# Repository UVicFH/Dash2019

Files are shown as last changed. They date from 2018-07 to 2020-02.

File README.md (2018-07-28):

# Dash2019

The purpose of this repository is to store the code and design files for the 2019 competition dash.

The newest CANduino revision will be used and the dash enclosure will house only a small PCB for the CANduino.

The project proposal, BOM, and other documentation can be found in the drive in Electrical/2018-2019/DASH

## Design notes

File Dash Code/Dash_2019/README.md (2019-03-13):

# Dashboard

This code runs the dashboard of the UVH19 vehicle. It takes the following message over CAN (bytes are in order starting at 0):

| Message | Bytes |
|---|---|
| RPM | 2 |
| 10*Coolant Temperature | 2 |
| SOC | 1 |
| Engine Running | 0.5 |
| RTD | 0.5 |
| Buzzer On | 1 |
| AMS Status | 0.5 |
| IMD Status | 0.5 |

This message should be sent at 5Hz from the supervisory controller and the message ID is defined in the defines.h file. 

It takes input from three buttons (engine start, motor start, and cockpit shutdown) and two analogs (Traction Control and Mode). These are indexed analog inputs.

It outputs to WS2812 addressable LED lights in 5 parts as shown below: 

| Name | Length |
|---|---|
| AMS Status | 1 |
| IMD Status | 1 |
| Engine Temperature | 1 |
| RPM	 | |
| Charge | 	 |

It also outputs the physical inputs over CAN in the following format at 5Hz:

| Message | Bytes | Format |
|---|---|---|
| Mode | 1 | Indexed 0-5 |
| Traction Control | 1 | 0-100 |
| Engine Start | 1 | 0/1 |
| Motor Start | 1 | 0/1 |
| CPBRB Status | 1 | 0/1 |

Please make sure the following library is installed before compiling: https://github.com/Seeed-Studio/CAN_BUS_Shield

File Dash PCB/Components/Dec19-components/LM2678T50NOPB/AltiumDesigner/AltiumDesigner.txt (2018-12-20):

# Created by Ultra Librarian Gold 8.3.15 Copyright © 1999-2018
# Frank Frank, Accelerated Designs

StartFootprints

Footprint (Name "TA07B")
Pad (Name "1") (Location -300, -441) (HoleSize 52) (Surface False) (Rotation 0) (ExpandMask 0)
PadShape (Size 72, 72) (Shape Rectangular) (Layer Top)
PadShape (Size 72, 72) (Shape Rectangular) (Layer Bottom)
PadShape (Size 72, 72) (Shape Rectangular) (Layer MidLayer)
EndPad
Pad (Name "2") (Location -250, -241) (HoleSize 52) (Surface False) (Rotation 0) (ExpandMask 0)
PadShape (Size 72, 72) (Shape Rounded) (Layer Top)
PadShape (Size 72, 72) (Shape Rounded) (Layer Bottom)
PadShape (Size 72, 72) (Shape Rounded) (Layer MidLayer)
EndPad
Pad (Name "3") (Location -200, -441) (HoleSize 52) (Surface False) (Rotation 0) (ExpandMask 0)
PadShape (Size 72, 72) (Shape Rounded) (Layer Top)
PadShape (Size 72, 72) (Shape Rounded) (Layer Bottom)
PadShape (Size 72, 72) (Shape Rounded) (Layer MidLayer)
EndPad
Pad (Name "4") (Location -150, -241) (HoleSize 52) (Surface False) (Rotation 0) (ExpandMask 0)
PadShape (Size 72, 72) (Shape Rounded) (Layer Top)
PadShape (Size 72, 72) (Shape Rounded) (Layer Bottom)
PadShape (Size 72, 72) (Shape Rounded) (Layer MidLayer)
EndPad
Pad (Name "5") (Location -100, -441) (HoleSize 52) (Surface False) (Rotation 0) (ExpandMask 0)
PadShape (Size 72, 72) (Shape Rounded) (Layer Top)
PadShape (Size 72, 72) (Shape Rounded) (Layer Bottom)
PadShape (Size 72, 72) (Shape Rounded) (Layer MidLayer)
EndPad
Pad (Name "6") (Location -50, -241) (HoleSize 52) (Surface False) (Rotation 0) (ExpandMask 0)
PadShape (Size 72, 72) (Shape Rounded) (Layer Top)
PadShape (Size 72, 72) (Shape Rounded) (Layer Bottom)
PadShape (Size 72, 72) (Shape Rounded) (Layer MidLayer)
EndPad
Pad (Name "7") (Location 0, -441) (HoleSize 52) (Surface False) (Rotation 0) (ExpandMask 0)
PadShape (Size 72, 72) (Shape Rounded) (Layer Top)
PadShape (Size 72, 72) (Shape Rounded) (Layer Bottom)
PadShape (Size 72, 72) (Shape Rounded) (Layer MidLayer)
EndPad
Line (Width 6) (Start -365, -118) (End -365, -487) (Layer Mechanical15) 
Line (Width 6) (Start -365, -487) (End 65, -487) (Layer Mechanical15) 
Line (Width 6) (Start 65, -487) (End 65, -118) (Layer Mechanical15) 
Line (Width 6) (Start 65, -118) (End -365, -118) (Layer Mechanical15) 
Polygon (PointCount 4) (Layer Mechanical15) 
Point (-365, -118)
Point (-365, -487)
Point (65, -487)
Point (65, -118)
EndPolygon
Line (Width 6) (Start -355, -173) (End 55, -173) (Layer TopOverlay) 
Line (Width 6) (Start -360, -318) (End 60, -318) (Layer TopOverlay) 
Line (Width 6) (Start 60, -318) (End 60, -123) (Layer TopOverlay) 
Line (Width 6) (Start 60, -123) (End -360, -123) (Layer TopOverlay) 
Line (Width 6) (Start -360, -123) (End -360, -318) (Layer TopOverlay) 
Arc (Width 6) (Radius 8) (Location -430, -441) (StartAngle 0) (EndAngle 360) (Layer TopOverlay) 
Line (Width 1) (Start -355, -178) (End 55, -178) (Layer Mechanical13) 
Line (Width 1) (Start -355, -313) (End 55, -313) (Layer Mechanical13) 
Line (Width 1) (Start 55, -313) (End 55, -128) (Layer Mechanical13) 
Line (Width 1) (Start 55, -128) (End -355, -128) (Layer Mechanical13) 
Line (Width 1) (Start -355, -128) (End -355, -313) (Layer Mechanical13) 
Arc (Width 0) (Radius 8) (Location -345, -303) (StartAngle 360) (EndAngle 720) (Layer Mechanical13) 
Text (Location -168.75, -165.5) (Height 25) (Width 1) (Rotation 0) (Layer Mechanical13) (Value "TAB")
Step (Name TA07B.stp)
EndFootprint

Footprint (Name "TA07Bm")
Pad (Name "1") (Location -300, -441) (HoleSize 52) (Surface False) (Rotation 0) (ExpandMask 0)
PadShape (Size 72, 72) (Shape Rectangular) (Layer Top)
PadShape (Size 72, 72) (Shape Rectangular) (Layer Bottom)
PadShape (Size 72, 72) (Shape Rectangular) (Layer MidLayer)
EndPad
Pad (Name "2") (Location -250, -241) (HoleSize 52) (Surface False) (Rotation 0) (ExpandMask 0)
PadShape (Size 72, 72) (Shape Rounded) (Layer Top)
PadShape (Size 72, 72) (Shape Rounded) (Layer Bottom)
PadShape (Size 72, 72) (Shape Rounded) (Layer MidLayer)
EndPad
Pad (Name "3") (Location -200, -441) (HoleSize 52) (Surface False) (Rotation 0) (ExpandMask 0)
PadShape (Size 72, 72) (Shape Rounded) (Layer Top)
PadShape (Size 72, 72) (Shape Rounded) (Layer Bottom)
PadShape (Size 72, 72) (Shape Rounded) (Layer MidLayer)
EndPad
Pad (Name "4") (Location -150, -241) (HoleSize 52) (Surface False) (Rotation 0) (ExpandMask 0)
PadShape (Size 72, 72) (Shape Rounded) (Layer Top)
PadShape (Size 72, 72) (Shape Rounded) (Layer Bottom)
PadShape (Size 72, 72) (Shape Rounded) (Layer MidLayer)
EndPad
Pad (Name "5") (Location -100, -441) (HoleSize 52) (Surface False) (Rotation 0) (ExpandMask 0)
PadShape (Size 72, 72) (Shape Rounded) (Layer Top)
PadShape (Size 72, 72) (Shape Rounded) (Layer Bottom)
PadShape (Size 72, 72) (Shape Rounded) (Layer MidLayer)
EndPad
Pad (Name "6") (Location -50, -241) (HoleSize 52) (Surface False) (Rotation 0) (ExpandMask 0)
PadShape (Size 72, 72) (Shape Rounded) (Layer Top)
PadShape (Size 72, 72) (Shape Rounded) (Layer Bottom)
PadShape (Size 72, 72) (Shape Rounded) (Layer MidLayer)
EndPad
Pad (Name "7") (Location 0, -441) (HoleSize 52) (Surface False) (Rotation 0) (ExpandMask 0)
PadShape (Size 72, 72) (Shape Rounded) (Layer Top)
PadShape (Size 72, 72) (Shape Rounded) (Layer Bottom)
PadShape (Size 72, 72) (Shape Rounded) (Layer MidLayer)
EndPad
Line (Width 6) (Start -365, -118) (End -365, -487) (Layer Mechanical15) 
Line (Width 6) (Start -365, -487) (End 65, -487) (Layer Mechanical15) 
Line (Width 6) (Start 65, -487) (End 65, -118) (Layer Mechanical15) 
Line (Width 6) (Start 65, -118) (End -365, -118) (Layer Mechanical15) 
Polygon (PointCount 4) (Layer Mechanical15) 
Point (-365, -118)
Point (-365, -487)
Point (65, -487)
Point (65, -118)
EndPolygon
Line (Width 6) (Start -355, -173) (End 55, -173) (Layer TopOverlay) 
Line (Width 6) (Start -360, -318) (End 60, -318) (Layer TopOverlay) 
Line (Width 6) (Start 60, -318) (End 60, -123) (Layer TopOverlay) 
Line (Width 6) (Start 60, -123) (End -360, -123) (Layer TopOverlay) 
Line (Width 6) (Start -360, -123) (End -360, -318) (Layer TopOverlay) 
Arc (Width 6) (Radius 8) (Location -430, -441) (StartAngle 0) (EndAngle 360) (Layer TopOverlay) 
Line (Width 1) (Start -355, -178) (End 55, -178) (Layer Mechanical13) 
Line (Width 1) (Start -355, -313) (End 55, -313) (Layer Mechanical13) 
Line (Width 1) (Start 55, -313) (End 55, -128) (Layer Mechanical13) 
Line (Width 1) (Start 55, -128) (End -355, -128) (Layer Mechanical13) 
Line (Width 1) (Start -355, -128) (End -355, -313) (Layer Mechanical13) 
Arc (Width 0) (Radius 8) (Location -345, -303) (StartAngle 360) (EndAngle 720) (Layer Mechanical13) 
Text (Location -168.75, -165.5) (Height 25) (Width 1) (Rotation 0) (Layer Mechanical13) (Value "TAB")
Step (Name TA07Bm.stp)
EndFootprint

Footprint (Name "TA07Bl")
Pad (Name "1") (Location -300, -441) (HoleSize 52) (Surface False) (Rotation 0) (ExpandMask 0)
PadShape (Size 72, 72) (Shape Rectangular) (Layer Top)
PadShape (Size 72, 72) (Shape Rectangular) (Layer Bottom)
PadShape (Size 72, 72) (Shape Rectangular) (Layer MidLayer)
EndPad
Pad (Name "2") (Location -250, -241) (HoleSize 52) (Surface False) (Rotation 0) (ExpandMask 0)
PadShape (Size 72, 72) (Shape Rounded) (Layer Top)
PadShape (Size 72, 72) (Shape Rounded) (Layer Bottom)
PadShape (Size 72, 72) (Shape Rounded) (Layer MidLayer)
EndPad
Pad (Name "3") (Location -200, -441) (HoleSize 52) (Surface False) (Rotation 0) (ExpandMask 0)
PadShape (Size 72, 72) (Shape Rounded) (Layer Top)
PadShape (Size 72, 72) (Shape Rounded) (Layer Bottom)
PadShape (Size 72, 72) (Shape Rounded) (Layer MidLayer)
EndPad
Pad (Name "4") (Location -150, -241) (HoleSize 52) (Surface False) (Rotation 0) (ExpandMask 0)
PadShape (Size 72, 72) (Shape Rounded) (Layer Top)
PadShape (Size 72, 72) (Shape Rounded) (Layer Bottom)
PadShape (Size 72, 72) (Shape Rounded) (Layer MidLayer)
EndPad
Pad (Name "5") (Location -100, -441) (HoleSize 52) (Surface False) (Rotation 0) (ExpandMask 0)
PadShape (Size 72, 72) (Shape Rounded) (Layer Top)
PadShape (Size 72, 72) (Shape Rounded) (Layer Bottom)
PadShape (Size 72, 72) (Shape Rounded) (Layer MidLayer)
EndPad
Pad (Name "6") (Location -50, -241) (HoleSize 52) (Surface False) (Rotation 0) (ExpandMask 0)
PadShape (Size 72, 72) (Shape Rounded) (Layer Top)
PadShape (Size 72, 72) (Shape Rounded) (Layer Bottom)
PadShape (Size 72, 72) (Shape Rounded) (Layer MidLayer)
EndPad
Pad (Name "7") (Location 0, -441) (HoleSize 52) (Surface False) (Rotation 0) (ExpandMask 0)
PadShape (Size 72, 72) (Shape Rounded) (Layer Top)
PadShape (Size 72, 72) (Shape Rounded) (Layer Bottom)
PadShape (Size 72, 72) (Shape Rounded) (Layer MidLayer)
EndPad
Line (Width 6) (Start -365, -118) (End -365, -487) (Layer Mechanical15) 
Line (Width 6) (Start -365, -487) (End 65, -487) (Layer Mechanical15) 
Line (Width 6) (Start 65, -487) (End 65, -118) (Layer Mechanical15) 
Line (Width 6) (Start 65, -118) (End -365, -118) (Layer Mechanical15) 
Polygon (PointCount 4) (Layer Mechanical15) 
Point (-365, -118)
Point (-365, -487)
Point (65, -487)
Point (65, -118)
EndPolygon
Line (Width 6) (Start -355, -173) (End 55, -173) (Layer TopOverlay) 
Line (Width 6) (Start -360, -318) (End 60, -318) (Layer TopOverlay) 
Line (Width 6) (Start 60, -318) (End 60, -123) (Layer TopOverlay) 
Line (Width 6) (Start 60, -123) (End -360, -123) (Layer TopOverlay) 
Line (Width 6) (Start -360, -123) (End -360, -318) (Layer TopOverlay) 
Arc (Width 6) (Radius 8) (Location -430, -441) (StartAngle 0) (EndAngle 360) (Layer TopOverlay) 
Line (Width 1) (Start -355, -178) (End 55, -178) (Layer Mechanical13) 
Line (Width 1) (Start -355, -313) (End 55, -313) (Layer Mechanical13) 
Line (Width 1) (Start 55, -313) (End 55, -128) (Layer Mechanical13) 
Line (Width 1) (Start 55, -128) (End -355, -128) (Layer Mechanical13) 
Line (Width 1) (Start -355, -128) (End -355, -313) (Layer Mechanical13) 
Arc (Width 0) (Radius 8) (Location -345, -303) (StartAngle 360) (EndAngle 720) (Layer Mechanical13) 
Text (Location -168.75, -165.5) (Height 25) (Width 1) (Rotation 0) (Layer Mechanical13) (Value "TAB")
Step (Name TA07Bl.stp)
EndFootprint
EndFootprints

StartComponents

Component (Name "LM2678T-5.0/NOPB") (PartCount 1) (DesPrefix "U?")
Pin (Location 300, 0) (Rotation 180) (PinType Output) (Length 300) (Width 0) (Designator Visible "1") (Name Visible "SW") (PinSwap 0) (PartSwap 0) (PinSeq 1) (Part 1)
Pin (Location 300, -100) (Rotation 180) (PinType Input) (Length 300) (Width 0) (Designator Visible "2") (Name Visible "Vin") (PinSwap 0) (PartSwap 0) (PinSeq 2) (Part 1)
Pin (Location 300, -200) (Rotation 180) (PinType Passive) (Length 300) (Width 0) (Designator Visible "3") (Name Visible "BOOST") (PinSwap 0) (PartSwap 0) (PinSeq 3) (Part 1)
Pin (Location 2500, -300) (Rotation 0) (PinType Passive) (Length 300) (Width 0) (Designator Visible "4") (Name Visible "GND") (PinSwap 0) (PartSwap 0) (PinSeq 4) (Part 1)
Pin (Location 2500, -200) (Rotation 0) (PinType Passive) (Length 300) (Width 0) (Designator Visible "5") (Name Visible "NC") (PinSwap 0) (PartSwap 0) (PinSeq 5) (Part 1)
Pin (Location 2500, -100) (Rotation 0) (PinType Passive) (Length 300) (Width 0) (Designator Visible "6") (Name Visible "FB") (PinSwap 0) (PartSwap 0) (PinSeq 6) (Part 1)
Pin (Location 2500, 0) (Rotation 0) (PinType Passive) (Length 300) (Width 0) (Designator Visible "7") (Name Visible "*ON/OFF") (PinSwap 0) (PartSwap 0) (PinSeq 7) (Part 1)
Rectangle (Width 5) (Start 300, 200) (End 2500, -500) (Part 1)
Parameter (Name "Manufacturer_Part_Number") (Location 0, 0) (Height 50) (Rotation 0) (Justification Center) (Value "LM2678T-5.0/NOPB") (Part 1)
Parameter (Name "Vendor") (Location 0, 0) (Height 50) (Rotation 0) (Justification Center) (Value "Texas Instruments") (Part 1)
Parameter (Name "Built_By") (Location 0, 0) (Height 50) (Rotation 0) (Justification Center) (Value "EMA_UL_Team") (Part 1)
Parameter (Name "RefDes") (Location 1400, 400) (Height 82) (Rotation 0) (Justification Center) (Value "RefDes") (Part 1)
Parameter (Name "Type") (Location 1400, 300) (Height 82) (Rotation 0) (Justification Center) (Value "DEV") (Part 1)
Parameter (Name "Value") (Location 1400, 300) (Height 82) (Rotation 0) (Justification Center) (Value "Value") (Part 1)
Parameter (Name "C") (Location 0, 0) (Height 1) (Rotation 0) (Justification Center) (Value "Copyright (C) 2015 Accelerated Designs. All rights reserved") (Part 1)
Comment (Value "Part Number: LM2678T-5.0/NOPB") (Part 1)
Footprint (Name "TA07B")
EndComponent
EndComponents

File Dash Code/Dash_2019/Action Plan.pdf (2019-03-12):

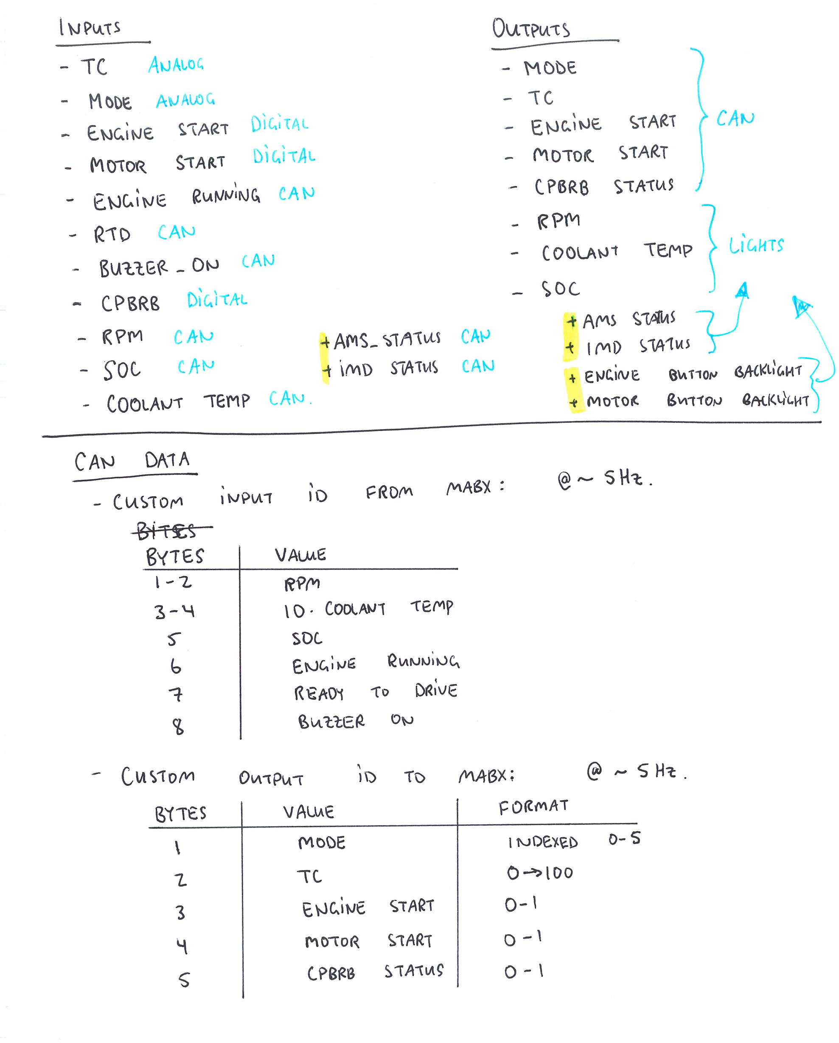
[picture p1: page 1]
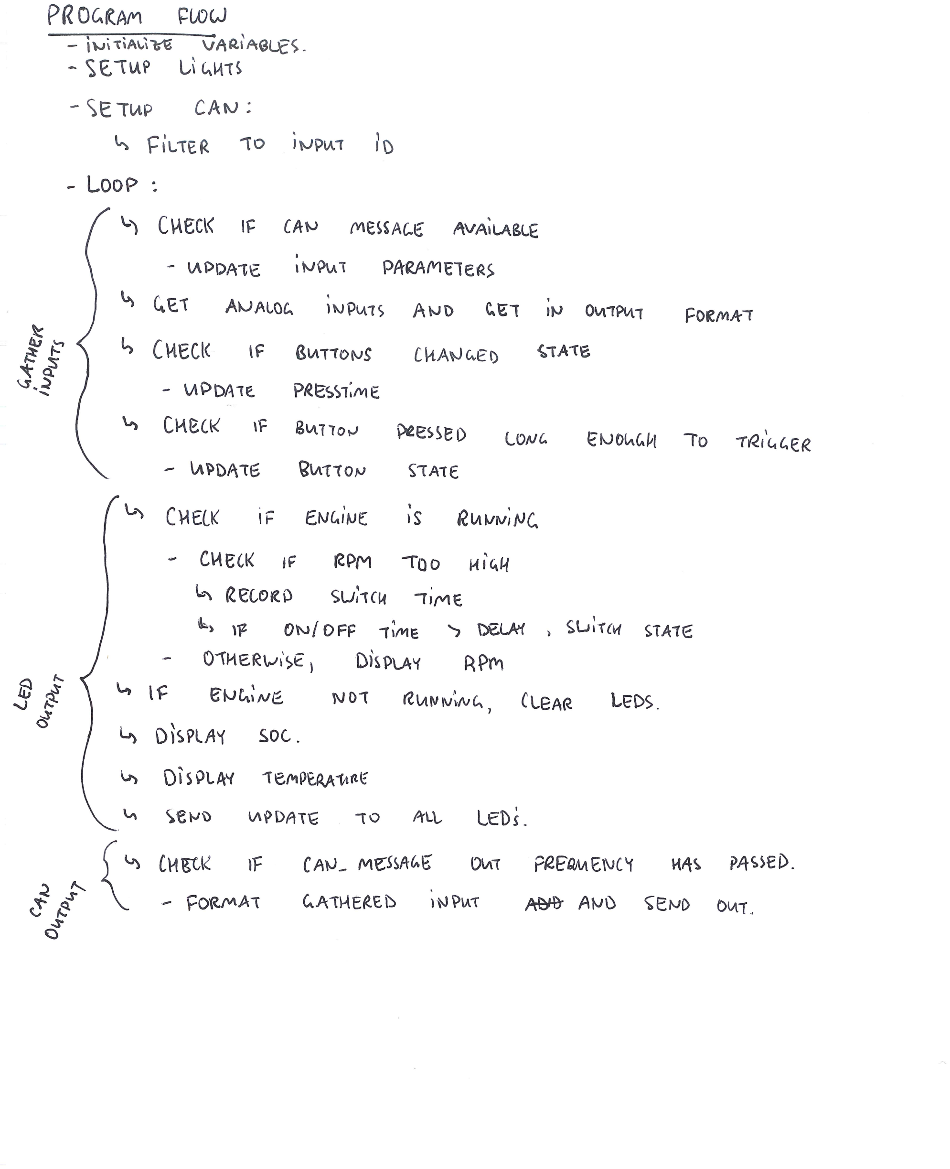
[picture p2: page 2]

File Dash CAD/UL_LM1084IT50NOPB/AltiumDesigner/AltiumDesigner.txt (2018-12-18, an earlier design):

# Created by Ultra Librarian Gold 8.3.15 Copyright © 1999-2018
# Frank Frank, Accelerated Designs

StartFootprints

Footprint (Name "T03B")
Pad (Name "1") (Location -200, -40) (HoleSize 54) (Surface False) (Rotation 0)
PadShape (Size 74, 74) (Shape Rectangular) (Layer Top)
PadShape (Size 74, 74) (Shape Rectangular) (Layer Bottom)
PadShape (Size 74, 74) (Shape Rectangular) (Layer MidLayer)
EndPad
Pad (Name "2") (Location -100, -40) (HoleSize 54) (Surface False) (Rotation 0)
PadShape (Size 74, 74) (Shape Rounded) (Layer Top)
PadShape (Size 74, 74) (Shape Rounded) (Layer Bottom)
PadShape (Size 74, 74) (Shape Rounded) (Layer MidLayer)
EndPad
Pad (Name "3") (Location 0, -40) (HoleSize 54) (Surface False) (Rotation 0)
PadShape (Size 74, 74) (Shape Rounded) (Layer Top)
PadShape (Size 74, 74) (Shape Rounded) (Layer Bottom)
PadShape (Size 74, 74) (Shape Rounded) (Layer MidLayer)
EndPad
Line (Width 6) (Start -317.5, -122.5) (End -317.5, 82.5) (Layer Mechanical15) 
Line (Width 6) (Start -317.5, 82.5) (End 117.5, 82.5) (Layer Mechanical15) 
Line (Width 6) (Start 117.5, 82.5) (End 117.5, -122.5) (Layer Mechanical15) 
Line (Width 6) (Start 117.5, -122.5) (End -317.5, -122.5) (Layer Mechanical15) 
Polygon (PointCount 4) (Layer Mechanical15) 
Point (-317.5, -122.5)
Point (-317.5, 82.5)
Point (117.5, 82.5)
Point (117.5, -122.5)
EndPolygon
Line (Width 6) (Start -312.5, -117.5) (End 112.5, -117.5) (Layer TopOverlay) 
Line (Width 6) (Start 112.5, -117.5) (End 112.5, 77.5) (Layer TopOverlay) 
Line (Width 6) (Start 112.5, 77.5) (End -312.5, 77.5) (Layer TopOverlay) 
Line (Width 6) (Start -312.5, 77.5) (End -312.5, -117.5) (Layer TopOverlay) 
Arc (Width 6) (Radius 8) (Location -382.5, -40) (StartAngle 0) (EndAngle 360) (Layer TopOverlay) 
Line (Width 6) (Start -210, -40) (End -190, -40) (Layer Mechanical13) 
Line (Width 6) (Start -200, -50) (End -200, -30) (Layer Mechanical13) 
Line (Width 1) (Start -307.5, -112.5) (End 107.5, -112.5) (Layer Mechanical13) 
Line (Width 1) (Start 107.5, -112.5) (End 107.5, 72.5) (Layer Mechanical13) 
Line (Width 1) (Start 107.5, 72.5) (End -307.5, 72.5) (Layer Mechanical13) 
Line (Width 1) (Start -307.5, 72.5) (End -307.5, -112.5) (Layer Mechanical13) 
Arc (Width 0) (Radius 8) (Location -287.5, -40) (StartAngle 360) (EndAngle 720) (Layer Mechanical13) 
Step (Name T03B.stp)
EndFootprint

Footprint (Name "T03Bm")
Pad (Name "1") (Location -200, -40) (HoleSize 54) (Surface False) (Rotation 0)
PadShape (Size 74, 74) (Shape Rectangular) (Layer Top)
PadShape (Size 74, 74) (Shape Rectangular) (Layer Bottom)
PadShape (Size 74, 74) (Shape Rectangular) (Layer MidLayer)
EndPad
Pad (Name "2") (Location -100, -40) (HoleSize 54) (Surface False) (Rotation 0)
PadShape (Size 74, 74) (Shape Rounded) (Layer Top)
PadShape (Size 74, 74) (Shape Rounded) (Layer Bottom)
PadShape (Size 74, 74) (Shape Rounded) (Layer MidLayer)
EndPad
Pad (Name "3") (Location 0, -40) (HoleSize 54) (Surface False) (Rotation 0)
PadShape (Size 74, 74) (Shape Rounded) (Layer Top)
PadShape (Size 74, 74) (Shape Rounded) (Layer Bottom)
PadShape (Size 74, 74) (Shape Rounded) (Layer MidLayer)
EndPad
Line (Width 6) (Start -317.5, -122.5) (End -317.5, 82.5) (Layer Mechanical15) 
Line (Width 6) (Start -317.5, 82.5) (End 117.5, 82.5) (Layer Mechanical15) 
Line (Width 6) (Start 117.5, 82.5) (End 117.5, -122.5) (Layer Mechanical15) 
Line (Width 6) (Start 117.5, -122.5) (End -317.5, -122.5) (Layer Mechanical15) 
Polygon (PointCount 4) (Layer Mechanical15) 
Point (-317.5, -122.5)
Point (-317.5, 82.5)
Point (117.5, 82.5)
Point (117.5, -122.5)
EndPolygon
Line (Width 6) (Start -312.5, -117.5) (End 112.5, -117.5) (Layer TopOverlay) 
Line (Width 6) (Start 112.5, -117.5) (End 112.5, 77.5) (Layer TopOverlay) 
Line (Width 6) (Start 112.5, 77.5) (End -312.5, 77.5) (Layer TopOverlay) 
Line (Width 6) (Start -312.5, 77.5) (End -312.5, -117.5) (Layer TopOverlay) 
Arc (Width 6) (Radius 8) (Location -382.5, -40) (StartAngle 0) (EndAngle 360) (Layer TopOverlay) 
Line (Width 6) (Start -210, -40) (End -190, -40) (Layer Mechanical13) 
Line (Width 6) (Start -200, -50) (End -200, -30) (Layer Mechanical13) 
Line (Width 1) (Start -307.5, -112.5) (End 107.5, -112.5) (Layer Mechanical13) 
Line (Width 1) (Start 107.5, -112.5) (End 107.5, 72.5) (Layer Mechanical13) 
Line (Width 1) (Start 107.5, 72.5) (End -307.5, 72.5) (Layer Mechanical13) 
Line (Width 1) (Start -307.5, 72.5) (End -307.5, -112.5) (Layer Mechanical13) 
Arc (Width 0) (Radius 8) (Location -287.5, -40) (StartAngle 360) (EndAngle 720) (Layer Mechanical13) 
Step (Name T03Bm.stp)
EndFootprint

Footprint (Name "T03Bl")
Pad (Name "1") (Location -200, -40) (HoleSize 54) (Surface False) (Rotation 0)
PadShape (Size 74, 74) (Shape Rectangular) (Layer Top)
PadShape (Size 74, 74) (Shape Rectangular) (Layer Bottom)
PadShape (Size 74, 74) (Shape Rectangular) (Layer MidLayer)
EndPad
Pad (Name "2") (Location -100, -40) (HoleSize 54) (Surface False) (Rotation 0)
PadShape (Size 74, 74) (Shape Rounded) (Layer Top)
PadShape (Size 74, 74) (Shape Rounded) (Layer Bottom)
PadShape (Size 74, 74) (Shape Rounded) (Layer MidLayer)
EndPad
Pad (Name "3") (Location 0, -40) (HoleSize 54) (Surface False) (Rotation 0)
PadShape (Size 74, 74) (Shape Rounded) (Layer Top)
PadShape (Size 74, 74) (Shape Rounded) (Layer Bottom)
PadShape (Size 74, 74) (Shape Rounded) (Layer MidLayer)
EndPad
Line (Width 6) (Start -317.5, -122.5) (End -317.5, 82.5) (Layer Mechanical15) 
Line (Width 6) (Start -317.5, 82.5) (End 117.5, 82.5) (Layer Mechanical15) 
Line (Width 6) (Start 117.5, 82.5) (End 117.5, -122.5) (Layer Mechanical15) 
Line (Width 6) (Start 117.5, -122.5) (End -317.5, -122.5) (Layer Mechanical15) 
Polygon (PointCount 4) (Layer Mechanical15) 
Point (-317.5, -122.5)
Point (-317.5, 82.5)
Point (117.5, 82.5)
Point (117.5, -122.5)
EndPolygon
Line (Width 6) (Start -312.5, -117.5) (End 112.5, -117.5) (Layer TopOverlay) 
Line (Width 6) (Start 112.5, -117.5) (End 112.5, 77.5) (Layer TopOverlay) 
Line (Width 6) (Start 112.5, 77.5) (End -312.5, 77.5) (Layer TopOverlay) 
Line (Width 6) (Start -312.5, 77.5) (End -312.5, -117.5) (Layer TopOverlay) 
Arc (Width 6) (Radius 8) (Location -382.5, -40) (StartAngle 0) (EndAngle 360) (Layer TopOverlay) 
Line (Width 6) (Start -210, -40) (End -190, -40) (Layer Mechanical13) 
Line (Width 6) (Start -200, -50) (End -200, -30) (Layer Mechanical13) 
Line (Width 1) (Start -307.5, -112.5) (End 107.5, -112.5) (Layer Mechanical13) 
Line (Width 1) (Start 107.5, -112.5) (End 107.5, 72.5) (Layer Mechanical13) 
Line (Width 1) (Start 107.5, 72.5) (End -307.5, 72.5) (Layer Mechanical13) 
Line (Width 1) (Start -307.5, 72.5) (End -307.5, -112.5) (Layer Mechanical13) 
Arc (Width 0) (Radius 8) (Location -287.5, -40) (StartAngle 360) (EndAngle 720) (Layer Mechanical13) 
Step (Name T03Bl.stp)
EndFootprint
EndFootprints

StartComponents

Component (Name "LM1084IT-5.0/NOP") (PartCount 1) (DesPrefix "U?")
Pin (Location 300, 0) (Rotation 180) (PinType Passive) (Length 300) (Width 0) (Designator Visible "1") (Name Visible "ADJ/GND") (PinSwap 0) (PartSwap 0) (PinSeq 1) (Part 1)
Pin (Location 2300, -100) (Rotation 0) (PinType Output) (Length 300) (Width 0) (Designator Visible "2") (Name Visible "Vout") (PinSwap 0) (PartSwap 0) (PinSeq 2) (Part 1)
Pin (Location 2300, 0) (Rotation 0) (PinType Input) (Length 300) (Width 0) (Designator Visible "3") (Name Visible "Vin") (PinSwap 0) (PartSwap 0) (PinSeq 3) (Part 1)
Rectangle (Width 5) (Start 300, 200) (End 2300, -300) (Part 1)
Parameter (Name "Manufacturer_Part_Number") (Location 0, 0) (Height 50) (Rotation 0) (Justification Center) (Value "LM1084IT-5.0/NOPB") (Part 1)
Parameter (Name "Vendor") (Location 0, 0) (Height 50) (Rotation 0) (Justification Center) (Value "Texas Instruments") (Part 1)
Parameter (Name "Built_By") (Location 0, 0) (Height 50) (Rotation 0) (Justification Center) (Value "EMA_UL_Team") (Part 1)
Parameter (Name "RefDes") (Location 1300, 400) (Height 82) (Rotation 0) (Justification Center) (Value "RefDes") (Part 1)
Parameter (Name "Type") (Location 1300, 300) (Height 82) (Rotation 0) (Justification Center) (Value "DEV") (Part 1)
Parameter (Name "Value") (Location 1300, 300) (Height 82) (Rotation 0) (Justification Center) (Value "Value") (Part 1)
Parameter (Name "C") (Location 0, 0) (Height 1) (Rotation 0) (Justification Center) (Value "Copyright (C) 2015 Accelerated Designs. All rights reserved") (Part 1)
Comment (Value "Part Number: LM1084IT-5.0/NOPB") (Part 1)
Footprint (Name "T03B")
EndComponent
EndComponents

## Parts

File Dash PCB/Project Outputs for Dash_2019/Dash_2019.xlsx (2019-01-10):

Comment | Description | Designator | Footprint | LibRef | Quantity | Supplier Part Number
4.7uF | Capacitor (Semiconductor SIM Model) | C1, C4, C6, C10 | CAPC3216X170N | Cap Semi | 4 | 1276-1055-1-ND
1uF | Capacitor (Semiconductor SIM Model) | C2, C5, C11 | CAPC3216X170N | Cap Semi | 3 | 1276-3086-1-ND
100nF | Capacitor (Semiconductor SIM Model) | C3, C7, C8, C9 | CAPC3216X170N | Cap Semi | 4 | 1276-1151-1-ND
10uF | Capacitor. Ceramic 10uF 50V rating recommended, place close to pin | C12, C13, C14 | CAPC3216X170N | Cap2 | 3 | 1276-1075-1-ND
Green | Typical RED, GREEN, YELLOW, AMBER GaAs LED | D1 | LEDC3216X120NGRN | LED2 | 1 | 732-4993-1-ND
Red | Typical RED, GREEN, YELLOW, AMBER GaAs LED | D2, D8 | LEDC3216X120NRED | LED2 | 2 | 732-4992-1-ND
Yellow | Typical RED, GREEN, YELLOW, AMBER GaAs LED | D3, D5, D6, D7 | LEDC3216X120NYEL | LED2 | 4 | 732-4994-1-ND
Diode | Default Diode | D4 | DO-220AA | Diode | 1 | SS1P3L-M3/84AGICT-ND
S1G-E3/61T | Surface Mount Glass Passivated Rectifier, 400 VDC, 1 A, -55 to 150 degC, 2-Pin SMD, RoHS, Tape and Reel | D9 | VISH-DO-214AC-SMA-2_N | S1G-E3/61T | 1 | S1G-E3/61TGICT-ND
Fuse 2 | Fuse | F1 | FUSC4632X85N | Fuse 2 | 1 | ‎MF-MSMF050-2CT-ND
USB micro B | CONN SM TH USB MICRO MODIFIED FOR DRILL | J1 | 1050170001 | 1050170001 | 1 | 609-4618-1-ND
ICSP | Header, 3-Pin, Dual row | P1 | Pin Header 2x3 TH Pitch 2.54mm | Header 3X2A | 1
4Pin Connector | Connector Header Through Hole 4 position 0.118" (3.00mm) 0430450413 | P2 | 4Pin connector Molex | 4Pin Connector | 1 | WM2649-ND
20Pin Connector | Connector Header Through Hole 20 position 0.118" (3.00mm) 43045-2013 | P3 | 20Pin connector Molex | 20Pin Connector | 1 | WM2657-ND
MOSFET-P | P-Channel MOSFET | Q1 | SOT23-3 | MOSFET-P | 1 | DMP3099L-7DICT-ND
MOSFET-N | N-Channel MOSFET | Q2 | SOT23-3 | MOSFET-N | 1 | SSM3K329RLFCT-ND
10K | Resistor | R1, R11 | RESC3216X60N | Res1 | 2 | RNCP1206FTD10K0CT-ND
1K | Resistor | R2, R3, R6, R7, R9, R12, R13, R14, R16, R17, R18, R19, R20, R21, R22, R23, R26 | RESC3216X60N | Res1 | 17 | RMCF1206FT1K00CT-ND
200Ohm | Resistor | R4, R5 | RESC3216X60N | Res1 | 2 | RNCP1206FTD200RCT-ND
16.9K | Resistor | R8 | RESC3216X60N | Res1 | 1 | RMCF1206FT16K9CT-ND
120 | Resistor | R10 | RESC3216X60N | Res1 | 1
268R | Resistor | R15 | RESC3216X60N | Res1 | 1 | RMCF1206FT267RCT-ND
511 | Resistor | R24 | RESC3216X60N | Res1 | 1 | RNCP1206FTD511RCT-ND
1206 | Resistor | R25, R27 | RESC3216X60N | Res1 | 2 | RHM1.0MPCT-ND
SW-PB | Switch | S1 | SMDswitch_1206 | SW-PB | 1 | CKN10779CT-ND
ATmega328P-AU | 8-bit AVR Microcontroller, 32KB Flash, 1KB EEPROM, 2KB SRAM, 32-pin TQFP, Industrial Grade (-40°C to 85°C) | U1 | QFP80P900X900X120-32N | ATmega328P-AU | 1 | ATMEGA328P-AU-ND
LM1117IMPX-5.0 | 800mA Low-Dropout Linear Regulator, 4-pin SOT-223 | U2 | SOT230P700X180-4N | LM1117IMPX-5.0 | 1 | 296-21114-1-ND
MCP2551-E/SN | SOIC | U3 | SOIC127P600X175-8N | MCP2551-E/SN | 1 | MCP2551T-E/SNCT-ND
FT232RL-Reel | USB UART Asynchronous Serial Data Transfer Chip, SSOP-28, Tape and Reel | U4 | SOP65P780X200-28N | FT232RL-Reel | 1 | 768-1007-1-ND
MCP2515-E/ST | SOIC | U5 | SOIC127P1030X265-18N | MCP2515-E/ST | 1 | MCP2515T-I/SOCT-ND
OKR-T10-W12-C | DC DC CONVERTER 0.591-6V 50W | U6 | OKR-T10-W12-C | OKR-T10-W12-C | 1 | 811-2180-ND
CSTCE16M0V53-R0 |  | Y1, Y2 | CSTCE_G | CSTCE16M0V53-R0 | 2 | 490-17948-1-ND

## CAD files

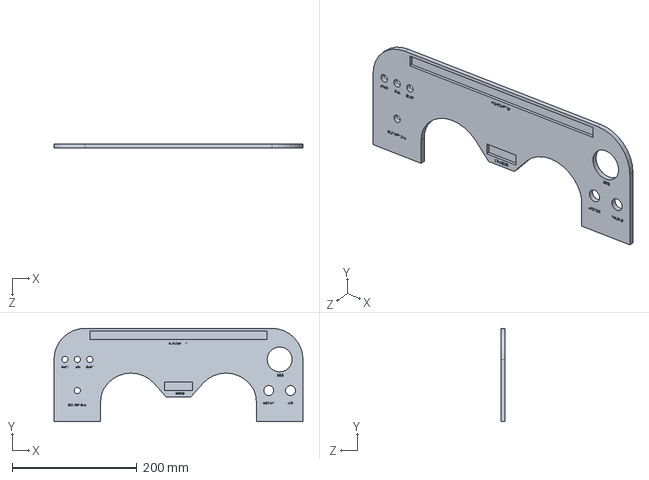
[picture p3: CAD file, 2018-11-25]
Dash CAD/Dashboard_V001.SLDPRT
400.0 x 150.0 x 6.35 mm

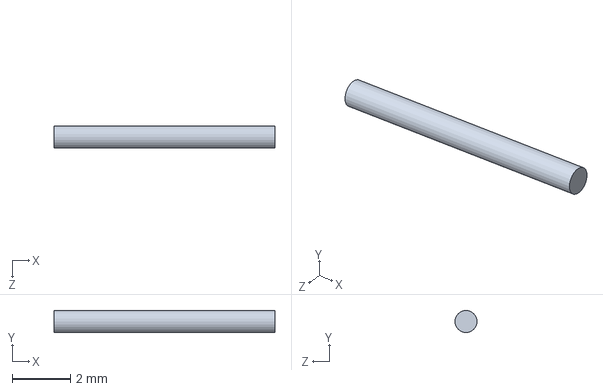
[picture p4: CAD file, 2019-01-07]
Dash CAD/DCDC/Pin.SLDPRT
7.62 x 0.762 x 0.762 mm

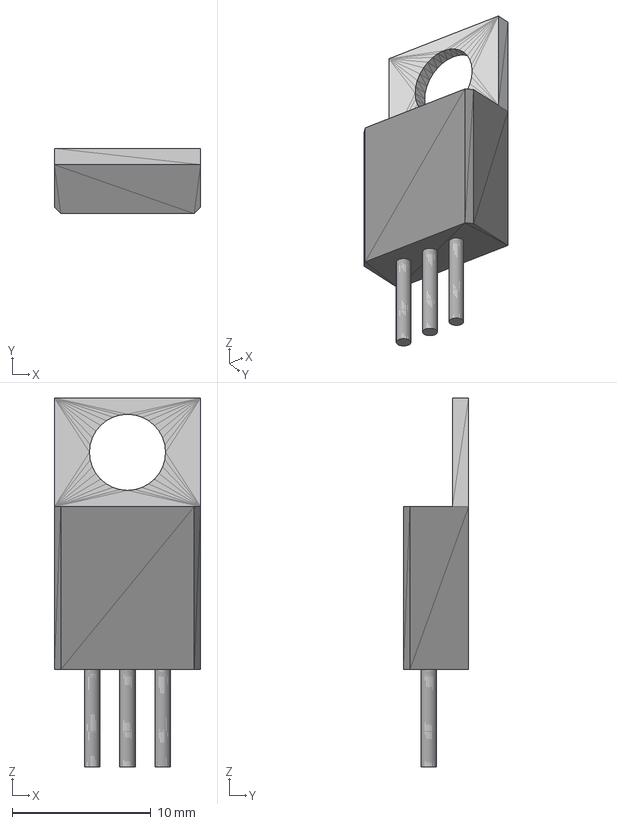
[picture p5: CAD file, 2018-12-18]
Dash CAD/UL_LM1084IT50NOPB/STL/T03Bm.stp
10.5 x 4.70 x 26.6 mm

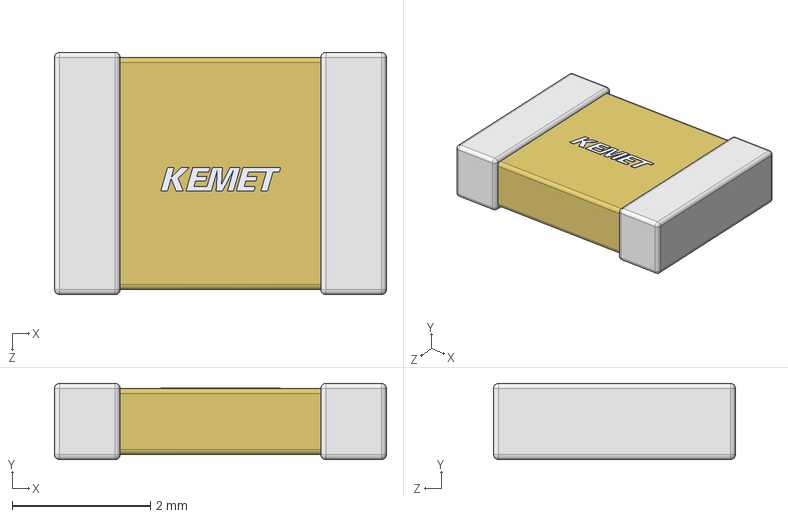
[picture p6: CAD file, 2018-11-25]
Dash PCB/Components/0.47uF Cap/C1812C474K5RACTU.step
4.80 x 1.10 x 3.50 mm

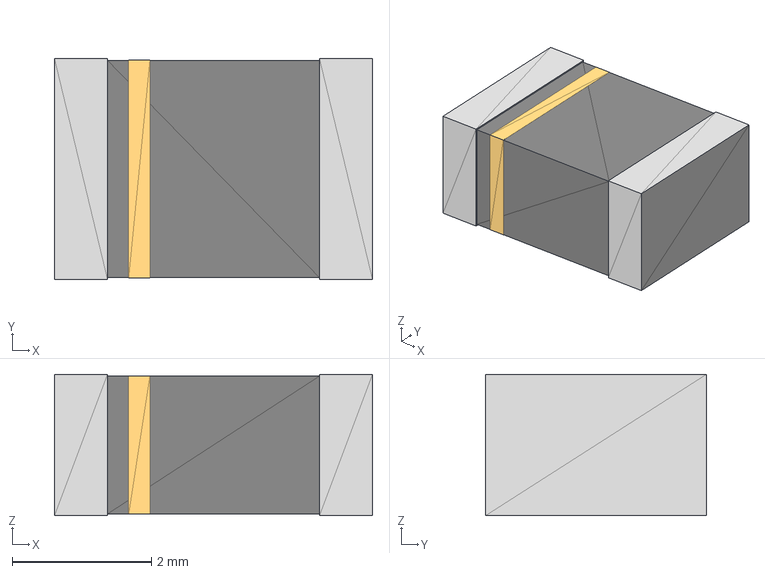
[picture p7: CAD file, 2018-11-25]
Dash PCB/Components/0.47uF Cap/STL/PCAP1812_Kemet.stp
4.57 x 3.18 x 2.03 mm

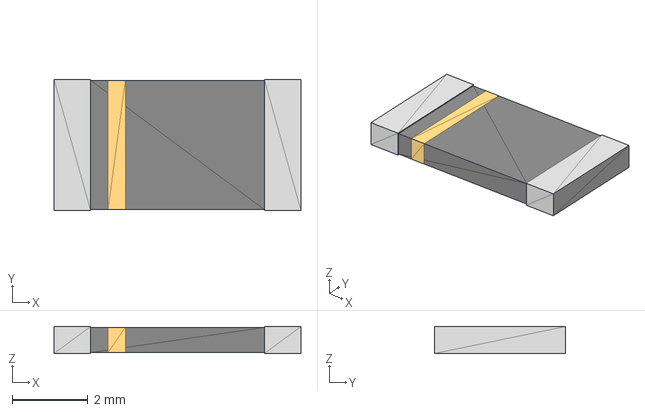
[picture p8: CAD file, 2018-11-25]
Dash PCB/Components/10kOhm/Correct/STL/STA_RMCF2512-M.stp
6.50 x 3.45 x 0.711 mm

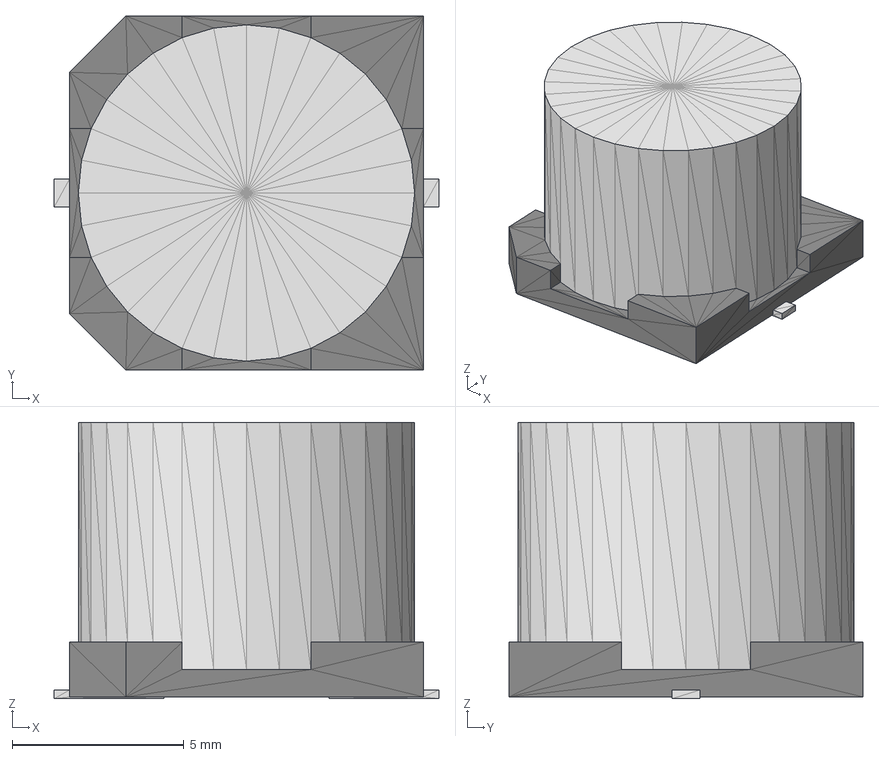
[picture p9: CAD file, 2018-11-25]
Dash PCB/Components/180uF Cap/STL/PCAP_SVP_F8-M.stp
11.2 x 10.3 x 8.05 mm

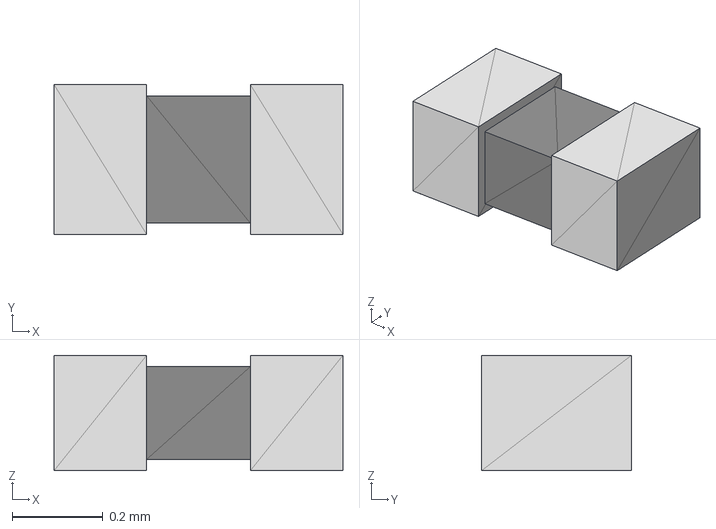
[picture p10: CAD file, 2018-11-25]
Dash PCB/Components/1KOhm Resistor/STL/YAG_R0201-M.stp
0.636 x 0.33 x 0.254 mm

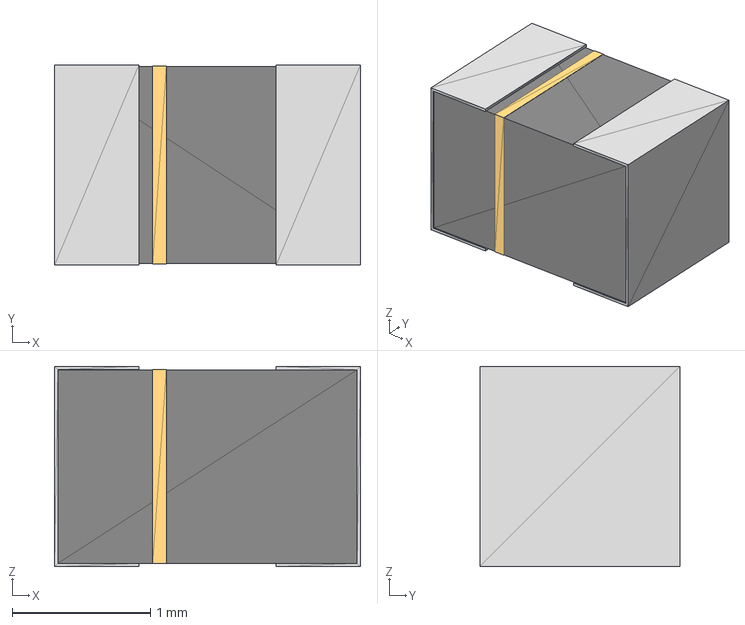
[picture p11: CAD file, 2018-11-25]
Dash PCB/Components/22uH Inductor/STL/IND_TAIYO_LBR2012.stp
2.21 x 1.45 x 1.45 mm

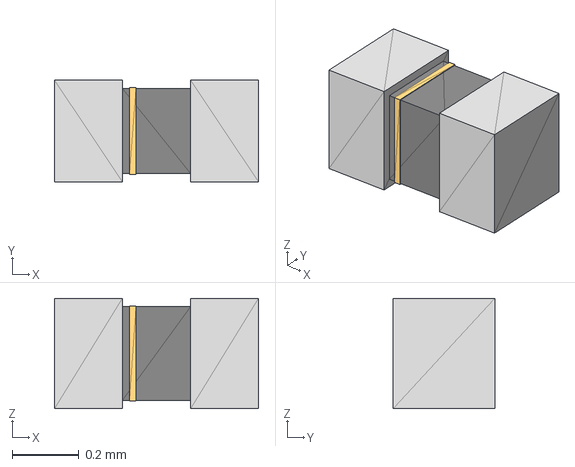
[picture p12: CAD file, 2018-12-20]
Dash PCB/Components/Dec19-components/0.01uF Capacitor/STL/G-033-M.stp
0.61 x 0.304 x 0.33 mm

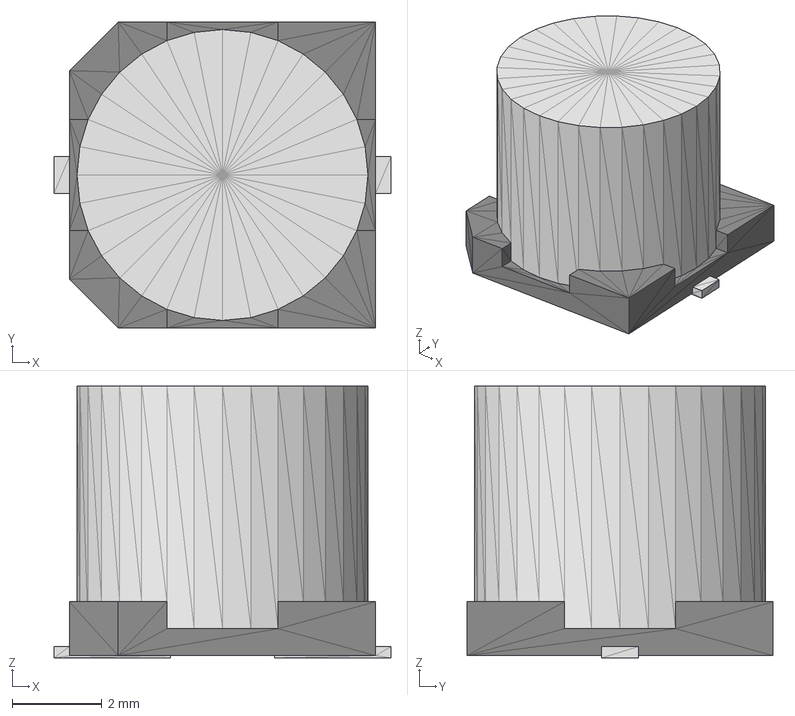
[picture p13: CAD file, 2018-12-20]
Dash PCB/Components/Dec19-components/180uF Capacitor/STL/PCAP_SVP_C6-M.stp
7.49 x 6.81 x 6.04 mm

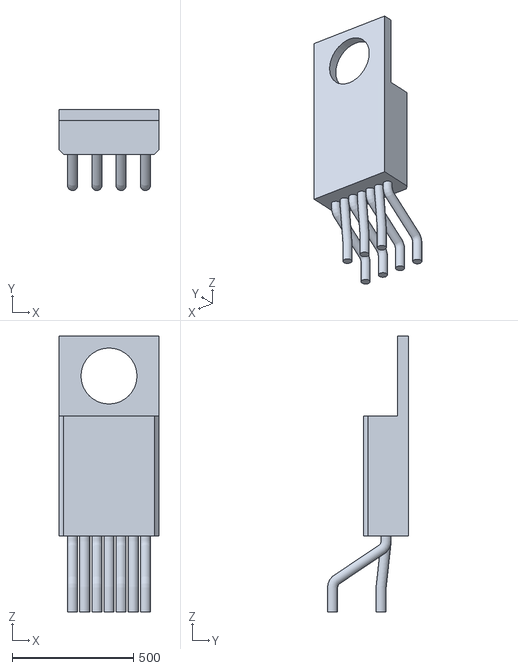
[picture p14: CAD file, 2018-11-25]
Dash PCB/Components/Dec19-components/LM2678T50NOPB/STL/TA07B.stl
410.0 x 334.0 x 1136.0

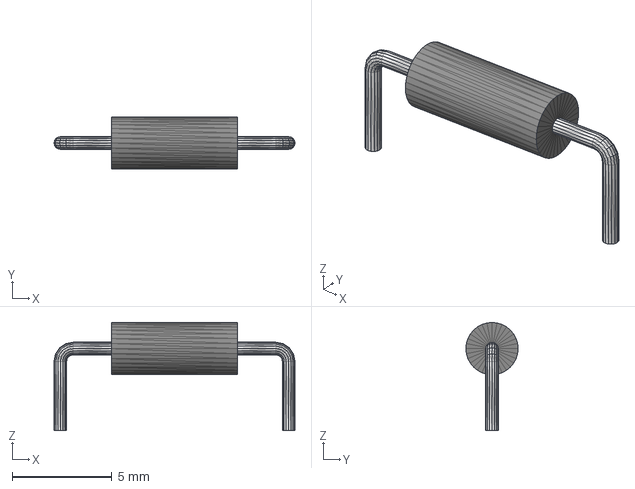
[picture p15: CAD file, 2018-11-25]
Dash PCB/Components/Generic Resistor/STL/STA_CF14.stp
12.1 x 2.62 x 5.41 mm

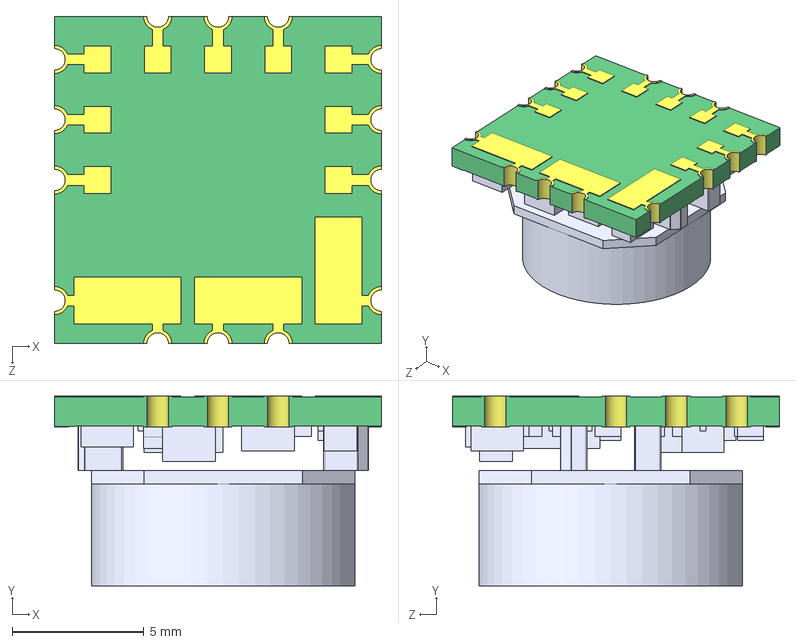
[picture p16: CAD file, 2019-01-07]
Dash PCB/Regulator Library/mps_dcdc_okl_t6_a.step
12.4 x 7.19 x 12.4 mm

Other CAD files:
Dash PCB/Components/Dec19-components/22uH Inductori/STL/IND_TAIYO_LBR2012.stp
Dash CAD/DCDC/mps_dcdc_okr_t10_w12_a.sldprt
Dash CAD/UL_LM1084IT50NOPB/STL/T03Bl.stp
Dash PCB/Components/0.47uF Cap/STL/PCAP1812_Kemet-M.stp
Dash CAD/DCDC/DCDC converter.SLDASM
Dash CAD/DCDC/DCDC converter.STEP
Dash CAD/UL_LM1084IT50NOPB/STL/T03B.stl
Dash CAD/UL_LM1084IT50NOPB/STL/T03B.stp
Dash CAD/UL_LM1084IT50NOPB/STL/T03Bl.stl
Dash CAD/UL_LM1084IT50NOPB/STL/T03Bm.stl
Dash PCB/Components/0.47uF Cap/STL/PCAP1812_Kemet-L.stl
Dash PCB/Components/0.47uF Cap/STL/PCAP1812_Kemet-L.stp
Dash PCB/Components/0.47uF Cap/STL/PCAP1812_Kemet-M.stl
Dash PCB/Components/0.47uF Cap/STL/PCAP1812_Kemet.stl
Dash PCB/Components/10kOhm/Correct/STL/STA_RMCF2512-L.stl
Dash PCB/Components/10kOhm/Correct/STL/STA_RMCF2512-L.stp
Dash PCB/Components/10kOhm/Correct/STL/STA_RMCF2512-M.stl
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

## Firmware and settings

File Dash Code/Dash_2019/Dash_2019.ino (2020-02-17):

  /*

Date:   12-Mar-2019
Author: Chad McColm

See README.md for more details

*/

// Include external library files
#include "Adafruit_NeoPixel.h"
#include "WS2812_Definitions.h"
#include <SPI.h>
#include <math.h>
#include "mcp_can.h"
#include <stdbool.h>

// Include internal definition library
#include "defines.h"

// Activate the CAN interface on its SPI select pin
MCP_CAN CAN(spiCsPin);

// Create an instance of the Adafruit_NeoPixel class
Adafruit_NeoPixel leds = Adafruit_NeoPixel(ledCount, ledPin, NEO_GRB + NEO_KHZ800);

// Global variables for input storage (global scope variables are initialized to 0)
int rpm;
float coolantTemperature;
int stateOfCharge;
bool engineRunning;
bool readyToDrive;
bool buzzerOn = 0;
bool amsStatus;
bool imdStatus;
bool launchActivated;
int mode;
int tractionControl;
bool engineStart = 1;
bool motorStart = 1;

// Global variables for debouncing inputs
bool lastEngineStartReading;
bool lastMotorStartReading;
unsigned long lastEngineStartReadingTime;
unsigned long lastMotorStartReadingTime;

// CAN frequency tracking
unsigned long canLastSent;

// Flash frequency tracking
unsigned long flashMode;

// DEMO mode variables
int temp_counter = 0;
int temp_counterrpm = 0;
int temp_dir = 1;
unsigned long LedClearTime;
int rpm_hold = 500;
unsigned long rpmHoldTime;
int temp_dirRpm = 1;

// This function runs on setup
void setup()
{

  // Initialize the led strip, set them all to off, and update the strip
  leds.begin();

  // Set all LEDs to off initially
  clearLEDs();
  leds.show();

  // Start up a serial interface in case any data needs to be sent to the connected PC
  Serial.begin(115200);

  // Initialize the CAN bus and stick into an error loop if that is not possible
  while (CAN_OK != CAN.begin(CAN_500KBPS)){
    Serial.println("CAN BUS Initialization Failed");
    delay(100);
  }
  Serial.println("CAN BUS Initialized OK!");

  pinMode(engineStartPin, INPUT_PULLUP);
  pinMode(motorStartPin, INPUT_PULLUP);

}

void loop(){

  if ((millis()-LedClearTime) >= 5000){
    clearLEDs();
    leds.show();
    LedClearTime = millis();
  }
  
  // DEMO mode
  if ((mode == 6) && (tractionControl == 6)){
    if (temp_dir) {
      temp_counter += 20;
    }
    else {
    temp_counter -= 20;
    }
    if (temp_dirRpm){
        temp_counterrpm += 100;
    } 
    else {
    temp_counterrpm -= 100;
    }
    if ( rpmHoldTime && ((millis()-rpmHoldTime) >=rpm_hold) ) {
      rpmHoldTime = 0;
      temp_dirRpm = 0;
    }
    
    if (temp_counterrpm >13000){
    temp_counterrpm = 13000;
    if (!rpmHoldTime) rpmHoldTime = millis();
    }
    if (temp_counterrpm <2000){
    temp_counterrpm = 2000;
    }
    // Process the message into the global input variables
    rpm = map(temp_counterrpm, 0, 13000, 0, 13000);
    coolantTemperature = map(temp_counter, 0, 13000, 0, 200);
    stateOfCharge = map(temp_counter, 0, 13000, 0, 100);
    engineRunning = 0;
    readyToDrive = 0;
    buzzerOn = 0;
    amsStatus = 0;
    imdStatus = 0;

    if (temp_counter>13000)
    {
      temp_dir =0;
    }
    else if (temp_counter<0)
    {
      temp_dir =1;
      temp_dirRpm = 1;
    }

  }
  // NORMAL mode
  else{
    // Update all inputs
    // Check if there is a CAN message available on the bus
    if(CAN_MSGAVAIL == CAN.checkReceive()){

      // Create a place to store the incoming CAN message
      unsigned char incomingMessageLength = 0;
      unsigned char incomingMessageData[8];
      unsigned long incomingMessageId = 0;

      // Save the CAN message and id
      CAN.readMsgBuf(&incomingMessageLength, incomingMessageData);
      incomingMessageId = CAN.getCanId();

      // Store things sent from MCU
      if(incomingMessageId == canInputIdMCU){

        // Process the message into the global input variables
        stateOfCharge = incomingMessageData[0];
        engineRunning = incomingMessageData[1] & 0b00000001;
        readyToDrive = (incomingMessageData[1] & 0b00000010) >> 1;
        buzzerOn = (incomingMessageData[1] & 0b00000100) >> 2;
        amsStatus = (incomingMessageData[1] & 0b00001000) >> 3;
        imdStatus = (incomingMessageData[1] & 0b00010000) >> 4;
        launchActivated = (incomingMessageData[1] & 0b00100000) >> 5;
        rpm = incomingMessageData[3] << 8 |incomingMessageData[2];

      }

      // Store things sent from Microsquirt (2)
      if(incomingMessageId == canInputIdCLT){

        // Process the message into the global input variables
        coolantTemperature = (incomingMessageData[6] << 8 | incomingMessageData[7])/10.0;

      }

    }
  }

  // If launch control is active then override the RPM bar with max to make it flash
  if(launchActivated){
    rpm = 12200;
  }

  // Update driver inputs

    // Update the analog inputs into the global input variables
    mode = round(analogRead(modePin)*5/1024.0)+1;
    tractionControl = round(analogRead(tractionControlPin)*5/1024.0)+1;

    // Get the current button state
    int engineStartReading = digitalRead(engineStartPin);
    int motorStartReading = digitalRead(motorStartPin);

    // If the reading has changed, reset the debounce timer
    if(engineStartReading != lastEngineStartReading)
      lastEngineStartReadingTime = millis();
    if(motorStartReading != lastMotorStartReading)
      lastMotorStartReadingTime = millis();

    // If the reading has been steady for longer than the delay, save that to the global variables
    if ((millis() - lastEngineStartReadingTime) > debounceDelay)
      engineStart = engineStartReading;
    if ((millis() - lastMotorStartReadingTime) > debounceDelay)
      motorStart = motorStartReading;

    // Update the last reading
    lastEngineStartReading = engineStartReading;
    lastMotorStartReading = motorStartReading;

  // Set all LED/buzzer outputs

    // Set the engine button light
    digitalWrite(engineLedPin, engineRunning);
    //if(engineRunning) Serial.println("engineRunning");

    // Set the motor button light
    digitalWrite(motorLedPin, readyToDrive);
    //if(readyToDrive) Serial.println("readyToDrive");

    // Set the buzzer to the inputted value
    digitalWrite(buzzerPin, buzzerOn);

    // Set the AMS Status LED
    leds.setPixelColor(amsLed, leds.Color(!amsStatus*255, 0, 0));

    // Set the IMD Status LED
    leds.setPixelColor(imdLed, leds.Color(!imdStatus*255, 0, 0));

    // Set the engine temperature LED based on temperature. Normal is off, low is green, hot is red
    if(coolantTemperature < coolantCold)
      leds.setPixelColor(coolantTemperatureLed, leds.Color(28, 135, 229));
    else if(coolantTemperature > coolantHot)
      leds.setPixelColor(coolantTemperatureLed, leds.Color(255, 0, 0));
    else
      leds.setPixelColor(coolantTemperatureLed, leds.Color(0, 0, 0));

    // Determine the correct color for the state of charge bar
    int stateOfChargeColor = round(stateOfCharge);

    // Loop through the bar's LEDs and set their color as required
    int i;
    for(i = 0; i < stateOfChargeLength; i++){
      if(i < stateOfCharge/100.0*stateOfChargeLength)
        leds.setPixelColor(i + stateOfChargeStart, HSBtoRGB(stateOfChargeColor,1,1));
      else
        leds.setPixelColor(i + stateOfChargeStart, 0);
    }

    // Determine the correct color for the state of RPM bar
    float rpmRatio = constrain(rpm/maxRpm, 0, 1);
    int rpmColor = round((1-rpmRatio)*120.0);

    // Loop through the bar's LEDs and set their color as required
    int j;
    int flasher = 1;
    
    if (rpm >= flashRpm){
      if ((millis()-flashMode) >= flashDelay){
        flasher = !flasher;
        flashMode = millis();
      }
      if (flasher){
        for(j = 0; j < rpmLength; j++){
           leds.setPixelColor(j + rpmStart, 0);
        }
      }
      else {
        for(j = 0; j < rpmLength; j++){
          if(j < rpmRatio*rpmLength){
            int flash = (flashMode / flashDelay) % 2;
            leds.setPixelColor(j + rpmStart, HSBtoRGB(rpmColor,1,1));
          }
          else
            leds.setPixelColor(j + rpmStart, 0);
          }
        }
    } else {
      for(j = 0; j < rpmLength; j++){
          if(j < rpmRatio*rpmLength){
            int flash = (flashMode / flashDelay) % 2;
            leds.setPixelColor(j + rpmStart, HSBtoRGB(rpmColor,1,1));
        }
        else
          leds.setPixelColor(j + rpmStart, 0);
        }
    }

  // Update the led changes just made
    Serial.println("RPM");
    Serial.println(rpm);
    leds.show();
    
  // Update all CAN outputs

    // Check if it's been long enough since the last CAN message was sent
    if(millis()-canLastSent > canDelay){

      // Build a new message
      uint8_t canMessage;
      canMessage = mode | tractionControl << 3 | !engineStart << 6 | !motorStart << 7;

      // Send the message
      CAN.sendMsgBuf(canOutputId, 0, 1, &canMessage);

      // Update the last send time
      canLastSent = millis();
    }

}

long HSBtoRGB(float _hue, float _sat, float _brightness) {
  float red = 0.0;
  float green = 0.0;
  float blue = 0.0;

  if (_sat == 0.0) {
    red = _brightness;
    green = _brightness;
    blue = _brightness;
  } else {
    if (_hue == 360.0) {
      _hue = 0;
    }

    int slice = _hue / 60.0;
    float hue_frac = (_hue / 60.0) - slice;

    float aa = _brightness * (1.0 - _sat);
    float bb = _brightness * (1.0 - _sat * hue_frac);
    float cc = _brightness * (1.0 - _sat * (1.0 - hue_frac));

    switch(slice) {
      case 0:
        red = _brightness;
        green = cc;
        blue = aa;
        break;
      case 1:
        red = bb;
        green = _brightness;
        blue = aa;
        break;
      case 2:
        red = aa;
        green = _brightness;
        blue = cc;
        break;
      case 3:
        red = aa;
        green = bb;
        blue = _brightness;
        break;
      case 4:
        red = cc;
        green = aa;
        blue = _brightness;
        break;
      case 5:
        red = _brightness;
        green = aa;
        blue = bb;
        break;
      default:
        red = 0.0;
        green = 0.0;
        blue = 0.0;
        break;
    }
  }

  long ired = red * 255.0;
  long igreen = green * 255.0;
  long iblue = blue * 255.0;

  return long((ired << 16) | (igreen << 8) | (iblue));

}

void clearLEDs()
{
  for (int i=0; i<ledCount; i++)
  {
    leds.setPixelColor(i, 0);
  }
}

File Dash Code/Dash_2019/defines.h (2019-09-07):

/* 

Here are where pins and message information is defined for the dashboard. 
More information can be found in README.md.

An excel file mirrors this information and has the same title. 

Author: Chad McColm
Date:   12-Mar-2019

*/
// Input CAN message
#define canInputIdMCU 100
#define canInputIdRPM 1520
#define canInputIdCLT 1522

// Output CAN message
#define canOutputId 90
#define canDelay 100

// Physical pins
#define spiCsPin 9
#define tractionControlPin A0
#define modePin A1
#define ledPin 3
#define engineStartPin 4
#define buzzerPin 5
#define motorStartPin 6
#define motorLedPin 7
#define engineLedPin 8

// Physical pin debouncing delay
#define debounceDelay 50

// LED Specifications
#define ledCount 57   //57
#define flashDelay 90

#define maxRpm 12300.0
#define flashRpm 11500.0
#define coolantCold 165
#define coolantHot 190

#define amsLed 0
#define imdLed 3
#define coolantTemperatureLed 6

#define stateOfChargeStart 49
#define stateOfChargeLength 8

#define rpmStart 7
#define rpmLength 42

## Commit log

2018-08-22 schematic updates
    Nas- dial connection, 20 pin connector, car connections
    [1206SMDswitch.PcbLib, BuzzerCircuit.SchDoc, CANduino_gyro.PcbLib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]
2018-08-23 finished up schematic
    Nas - finished buzzer schematic
    still need to assign a few arduino pins and figure out the libraries for the parts, spec the linear regulator and the logic level mosfets
    [Candunio.SchDoc, DashNas.SchDoc, Dash_PCB_Nas.PrjPCB]
2018-08-23 removed file
    removed blank file as we decided on addressable LEDs for the display
    [LCDDisplay.SchDoc]
2018-08-24 dash updated (8/23/18)
    [Candunio.SchDoc, DashNas.SchDoc]
2018-09-11 minor changes
    [DashNas.SchDoc, Dash_PCB_Nas.PrjPCB]
2018-11-25 Tracks started
    Started tracks between components
    [0.PcbLib, 0.SchLib, 10000pF-Cap.PcbLib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]
2018-11-25 push 15uF cap changes
    See title
    [15uF-Cap.PcbLib, 15uF-Cap.SchLib, U2-I-L.stl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]
2018-11-28 Track progress
    track progress. Need some advice for routing.
    [Dash_PCB_Nas.PrjPCB]
2018-12-18 Revisions 12/17
    Have to revise current regulator componets/circuit w/ ash
    [Candunio.SchDoc, DashNas.SchDoc]
2018-12-18 Schematic changes
    -updated regulator
    -changed buzzer circuit
    -changed diode footprint
    [AltiumDesigner.PcbLib, AltiumDesigner.SchLib, Candunio.SchDoc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]
2018-12-19 saved before not responding
    track layout begun
2018-12-19 Routed traces
    routed traces - need to check
    [Dash_PCB_Nas.PrjPCB]
2018-12-20 need to change to switching regulator
    see above
    [AltiumDesigner.PcbLib, AltiumDesigner.SchLib, DashNas.SchDoc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]
2019-01-03 CAD updated for dcdc
    [DCDC converter.SLDASM, DCDC converter.STEP, Pin.SLDPRT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]
2019-01-03 Colors woo
    [DCDC converter.STEP]
2019-01-07 V1 completed ready to review
    Switching power supply added for LED strip.
    component parts chosen and libraries fixed.
    PCB layed and complete.
    [430450413.stp, 430452013.stp, AltiumDesigner.SchLib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]
2019-01-10 Design reviewd, changed made, V1
    changed c12,13,14 to non polarized caps
    added extra ground stiching
    [Dash.SchDoc, Dash_2019.PrjPCB, Dash_2019.xlsx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]
2019-01-10 ready for order
    [Dash2019.DRL, Dash2019.GBL, Dash2019.GBO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]
2019-02-15 started code
    defined pins and CAN IDs, added LED Tach code and test code. Needs editing
2019-03-13 Bug fixes. Code now compiles
    [Dash_2019.ino, defines.h]
2019-03-24 code updates
    correct LED and button code
    [Dash_2019.ino, Dash_Test.ino, defines.h]
2019-04-19 updated length of led strip
2019-09-07 Eidien-ness Switch
    Switched eidienness where necessary.
2019-09-08 Debugin dash
    fixing LED freeze issue attempt 1
    [Dash_2019.ino]
